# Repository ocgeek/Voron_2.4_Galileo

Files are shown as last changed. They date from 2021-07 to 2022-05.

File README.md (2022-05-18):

**Galileo Clockwork**

Please go to the original repository for Galileo Clockwork (as it is actively maintened there)
https://github.com/JaredC01/Galileo

**Galileo driven Z-Drives**

The source components are from the great **project and design** of **JaredC01** (see Voron Discord)

**Mind that these components are by design of the author a TIGHT FIT** 
Some pressing in of the bearings is expected and IMHO intended.
I used a long exagonal key driver (M10) to press them in by my body weight..

You can reach out in Voron Discord i'm **oc_geek V2.1064 V2.1820**

This is goint to be my second Voron 2.4 build 
and il will be equipped with Galileo Z Gearboxes and Galileo Extruder (and few other mods :-) ) 

I made some chages to his design (was tailored for Voron 2.2 in ~ 2020)
- Fixed the hole height of M5x40 screw to grab 5mm on the M5 post insert nut
- The Mount has a larger center hole (now ID is 8.6mm) to allow the bearing removal and avoid D shaft rubbing plastic
- Reduced the 4xM3 holes in the Mount to ID 3.4 mm (from 4.2) for a snug alignment to the Gearbox shelve
- The Mount (aka Foot) is now 10 mm taller to better suite a V2.4 build bottom height (it does not change the belts lenght)
- Stepper Spacer has now a hook (with M5x20 BH) to the inner frame extrusion so stepper Motor weight does not load on Gearbox. A hole for the M3 pass through screw has been added to the spacer for mounting the Gearbox shelve
- Added skirts for V2.4 300mm including a rotating gear (pressure) mounted on the D-Shaft protruding out of Mount front (~ 3mm)

I developed all those changes in **Fusion 360**
The **CAD file** is too large to store here 
i uploaded it on Google Drive (lates update 11st July 2021) [Z Drive f3z archive](https://drive.google.com/drive/folders/1R-tB0uDWe6UOru6ewyngyY7uPnOx-Cvc?usp=sharing)

**Z Gearbox** BOM
_Quantity is for ONE (1) Gearbox_
- 10T metal Spur Gear x1 - <<https://www.aliexpress.com/item/4000299898525.html>>
- 5x4mm Heat inserts x8 (Voron BOM)
- 60mm Long 5mm OD D-shaft (Voron BOM)
- 16T "Prusa Stile" Pulley with Base H=6mm (thinner than POWGE) x1 - e.g. <<https://www.amazon.it/gp/product/B07T5CYBJW/ref=ppx_yo_dt_b_search_asin_title?ie=UTF8&psc=1>>
- 1.0mm shim M5 washers x2 (or 0.5mm if you wanna play finer) 
- F695 2RS Bearing x4 (Carrier and Gearbox)
- F625 2RS Bearing x1 (Mount)
- M3x12mm SHCS screws x4 (to close the gear Shelves)
- M5x16mm BHCS screws x3 (gears to carrier)
- M3x18mm SHCS screws x4 (connect to the Stepper)
- M3x20mm SHCS screws x4 (connect Mount to gear Front Housing)

Mounting a Z-Drive to the frame requires:
- M5x40mm SHCS screw x1 (Mount part to Frame from where the rubber foot is)
- M5x16mm BHCS screws x2 (Mount part bottom two holes to Frame)
- M5x20mm BHCS screws x1 (Accent Spacer to Frame)

See in the **Assembly folder** there are some notes on how i did put these things together :)



These are the assembled GearBoxes



I modified the spacer so that it hooks onto the frame and sustains the Stepper weight. 
Also it sists in the center of mass of the assembly
This is reccomended works very well



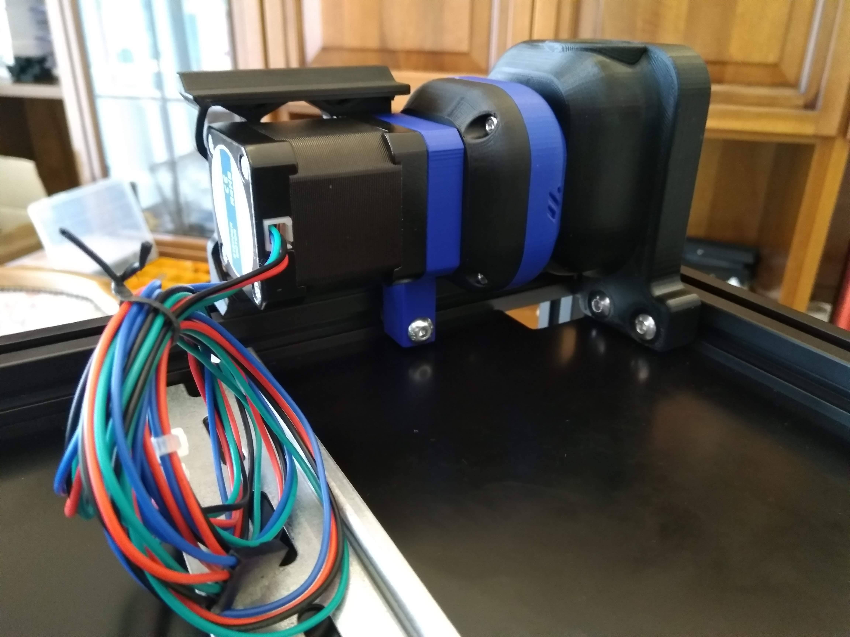
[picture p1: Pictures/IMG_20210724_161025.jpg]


I amended the Mount (foot) to be 10mm taller and better suited to the Voron 2.4 (the change does not change the belt lenghts) 









IMG_20210814_064714 (1)



**This is a list of what i ended up installing in this build :)**

**Frame and Panels:**
- 4mm thick polycarbonate panels (including the bottom deck to view through the electronics)
- Doors with hinges
- Handles 2x on top and 2x at bottom sides (it's 50Kg this thing...)

**Control Electronics and cabling**
- Duet Mini 5+ Wifi
- Duet 2+ expansion (to reach 7 drivers)
- Prepared for an additional Duet 5+ (not yet installed for ERCF MMU unit - future) via FD-CAN bus
- Duet Tool Board 1LC (v1.1 with included accelerometer) mounted on the tool head side and connected via FD-CAN bus
- Heluflon FEP wires (AWG 18, 20, 24)
- MDPC-X sleeve (used out of the chains)
- Wago 221 connectors
- Chamber temp / humidity sensor (DHT21)
- Ambient temp thermistor
- Various cable management brackets (made in Fusion360) and cables routing guide out of the cables hole in the back

**Mechanics and movement:**
- OMC Steppers-online motors
- 1.8* on Z axis (4)
- 0.9* on X-Y axis (2)
- LDO pancake for Galileo Clockwork Extruder
- Galileo gear-boxes for Z movement (required redesign of the entire skirts)
- Galileo Clockwork (Coupler Edition) for Extruder
- MGN-12 single rail on X axis
- AB-BN 30 tool body with 5015 work cooling fan
- Hall effect end stops for X/Y
- MGC5 spherical Z joints
- Klicky probe (instead of the inductive Z sensor) for bed leveling and final Z0 setting
- Pin mod on all bearings / idlers (5mm pins replace M5 screws - requires specific printed parts)

**Air Filtering**
- Nevermore Micro recirculating active carbon filter (dual 5015 fan located under the heated bed; also serves as quick chamber heat distribution in the pre-print phase)

**Lights:**
- WS2811 (aka neopixel) addressable LED strips with controllable brightness and color for each LED on each strip
- 15 LEDs on front, 18 LEDs each side top

**Others:**
- Purge bucket with scrub
- Align stands for the steel flex plate (two embedded in the Purge bucket body)

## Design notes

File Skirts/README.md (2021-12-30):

One note on the skirts...

Remind to install the **Side Skirt BEFORE** you install the Galileo GearBox itself... don't ask how do i know that...

You are adviced

These skirts are my design and will fit on a **Voron 2.4 300**



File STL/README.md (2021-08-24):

Here i uploaded the STL files for the Galileo GearBoxes 
and also the other Mods which i did implement. 

Some of the Mods (e.g. Pinned and Spherical Joints) intersect and need specific STL(s) 
making the search of the proper files a challenge

So here they are all together

:)

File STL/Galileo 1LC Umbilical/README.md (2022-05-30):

STLs for umbilical mount for 1LC Duet (or fysect) 1.1 and above toolboard

Files ARE NOT oriented for printing so please arrange them properly on plate









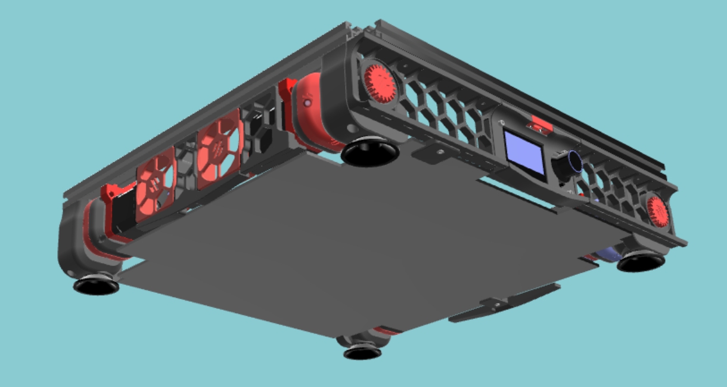
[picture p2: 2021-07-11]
Pictures/Bottom.jpg

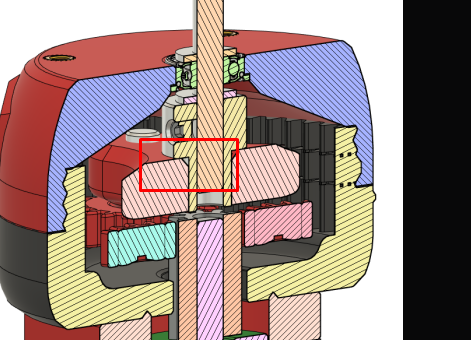
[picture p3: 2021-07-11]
Pictures/unknown.png

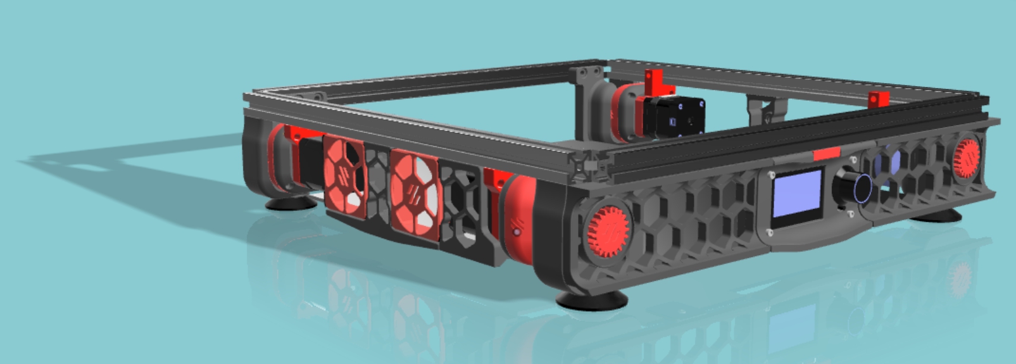
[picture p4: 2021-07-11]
Pictures/Front.jpg

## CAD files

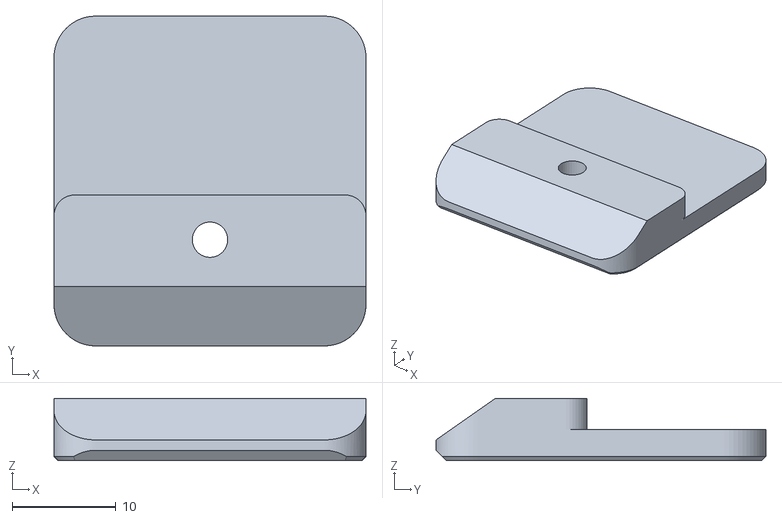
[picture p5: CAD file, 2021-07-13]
Skirts/Galileo 3mm Panel Clip x4.stl
30.0 x 31.7 x 6.00

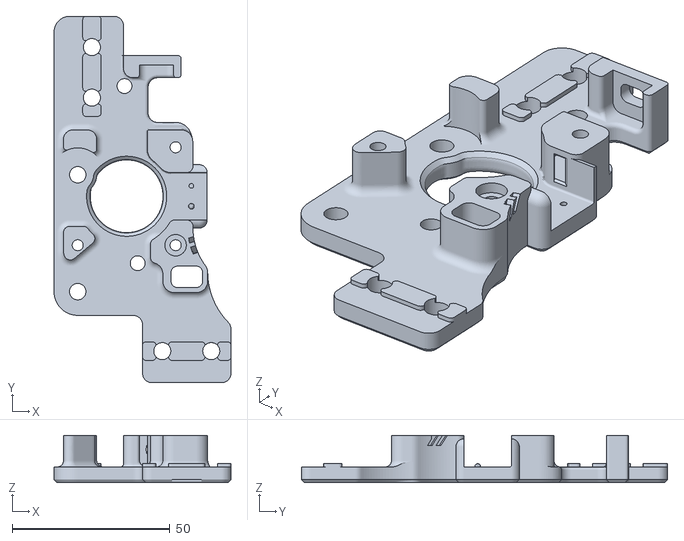
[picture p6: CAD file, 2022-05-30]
STL/Galileo 1LC Umbilical/a_drive_frame_upper_with_jst_y_endstop.stl
56.0 x 116.0 x 15.0

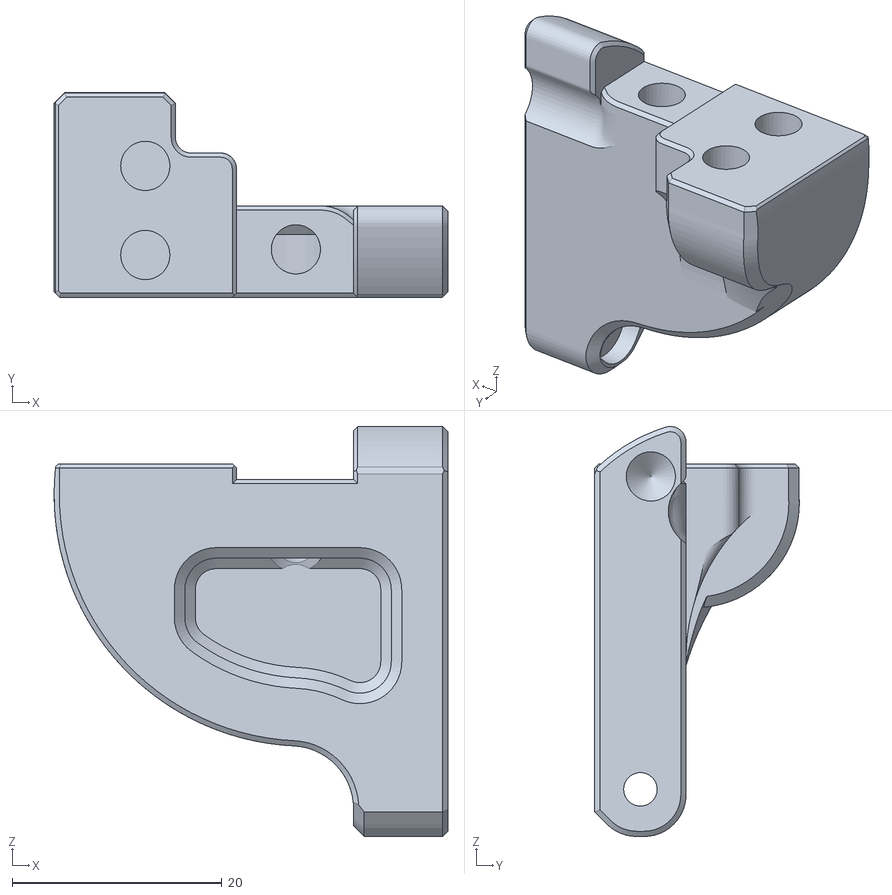
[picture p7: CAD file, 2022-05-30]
STL/Galileo 1LC/Chain anchor IGUS Backers.stl
37.6 x 19.5 x 39.1

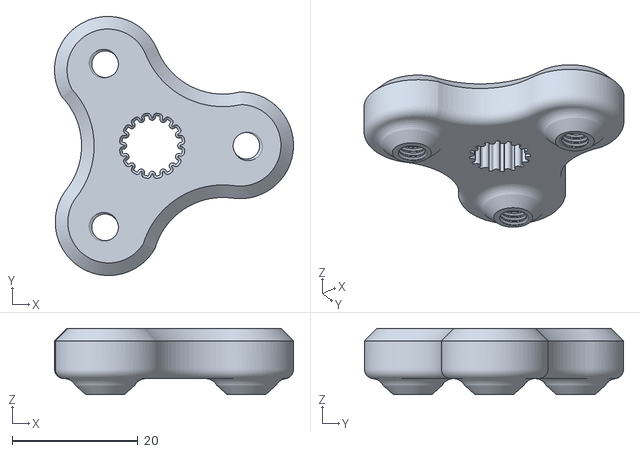
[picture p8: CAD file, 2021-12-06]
STL/GearBox Galileo/Carrier x4.stl
38.1 x 41.2 x 10.6

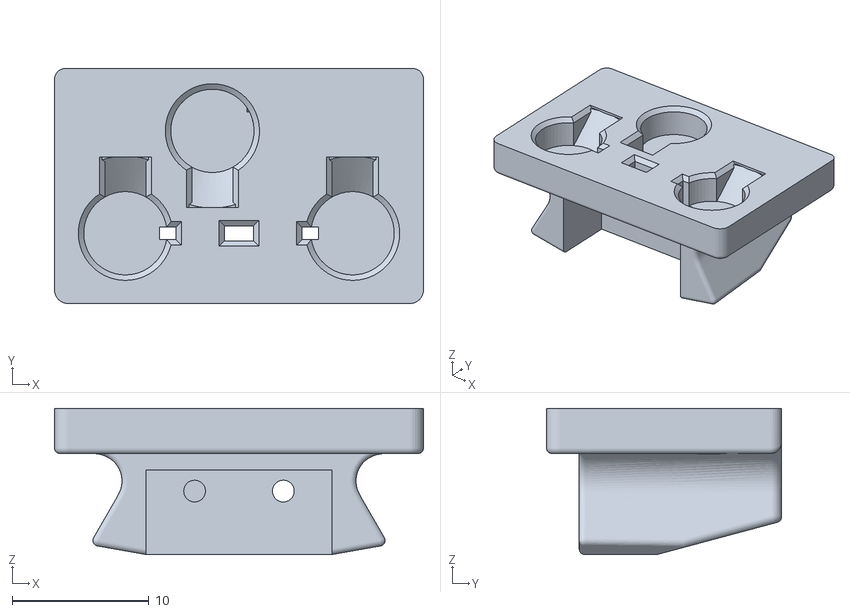
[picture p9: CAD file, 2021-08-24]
STL/Klicky for MGN12/New Probe V2 Angled.stl
27.0 x 17.2 x 10.7

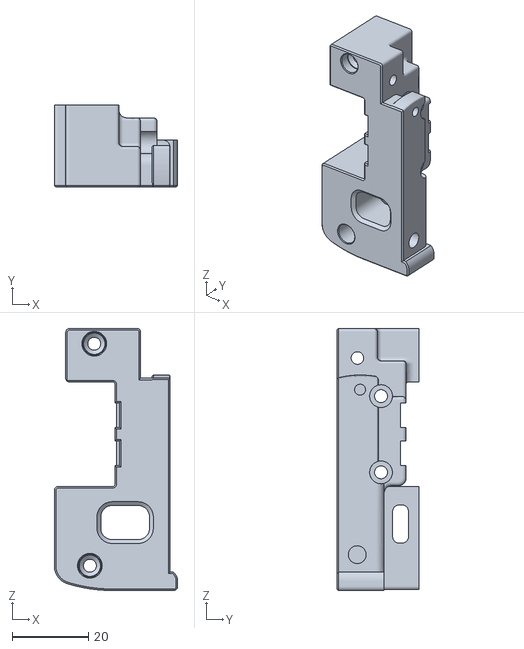
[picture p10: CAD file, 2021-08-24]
STL/MGN12 rail and Pinned Mod/x_carriage_frame_left 210729.stl
32.4 x 21.6 x 68.8

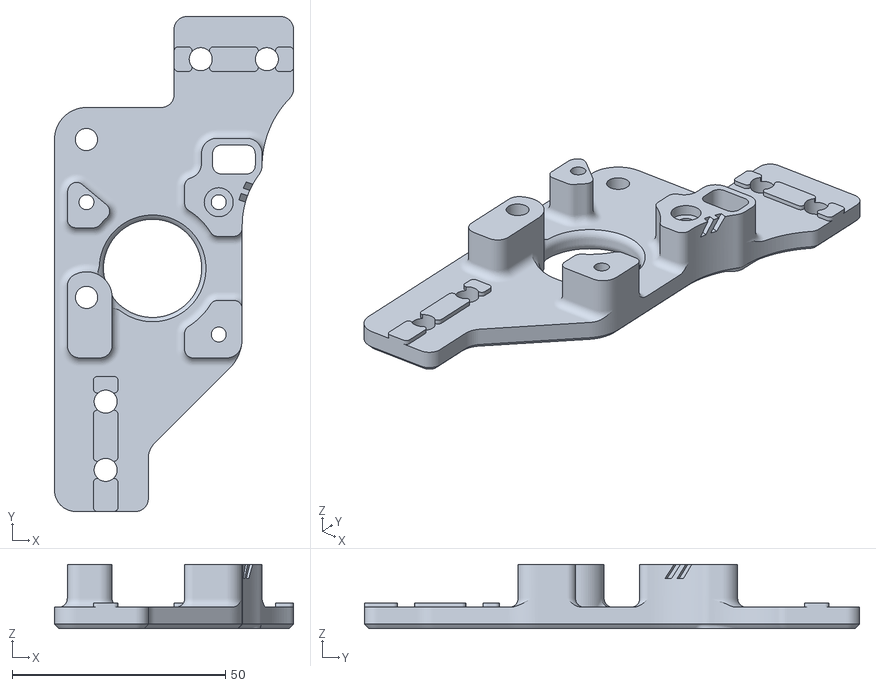
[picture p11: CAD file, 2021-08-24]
STL/Spherical Joints MGC5 and Pinned Mod/b_drive_frame_upper_pinned.stl
56.0 x 116.0 x 15.0

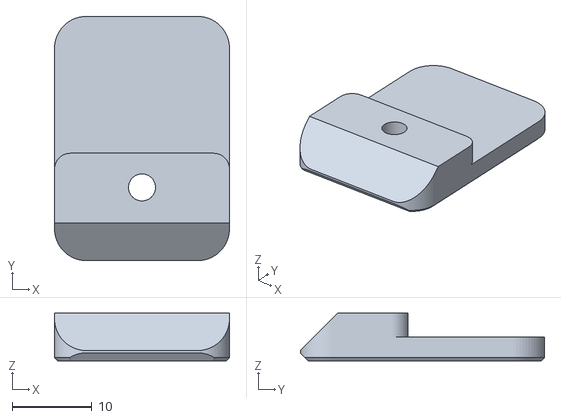
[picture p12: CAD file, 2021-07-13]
Skirts/Galileo 3mm Panel Clip Slim x2.stl
22.0 x 30.7 x 6.00

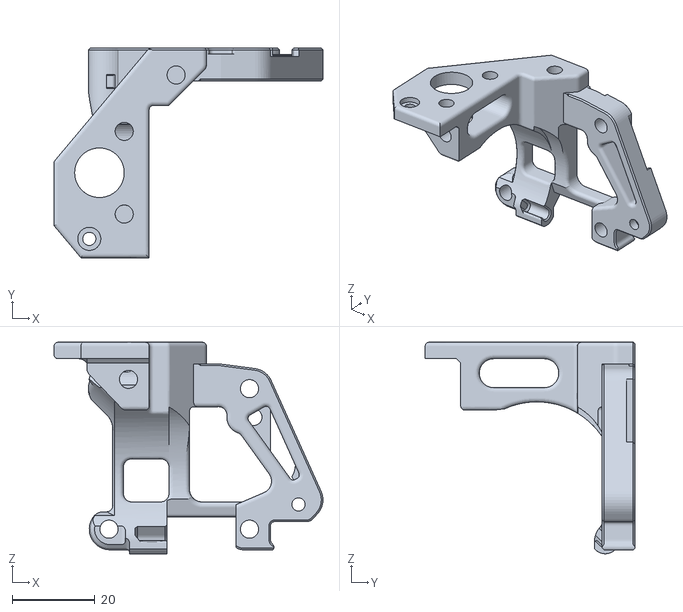
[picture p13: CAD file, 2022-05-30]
STL/Galileo 1LC Umbilical/Galileo 1LC PCB Holder Umbilical.stl
65.1 x 50.8 x 51.2

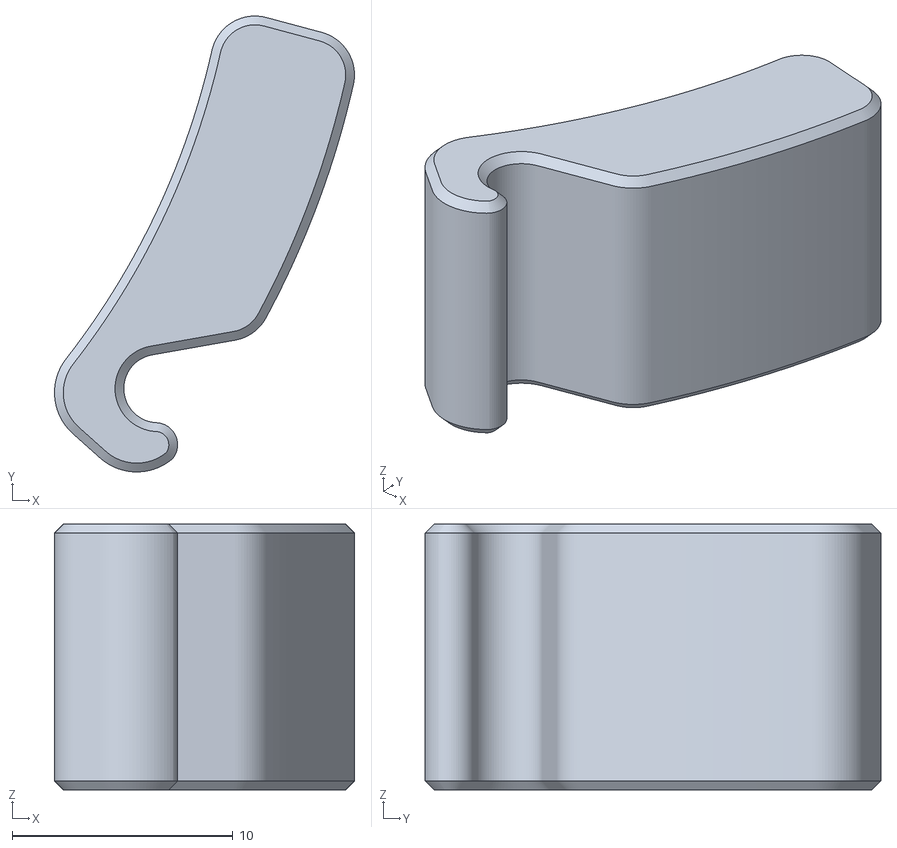
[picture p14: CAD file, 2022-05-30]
STL/Galileo 1LC/[a]_latch_shuttle.stl
13.6 x 20.7 x 12.0

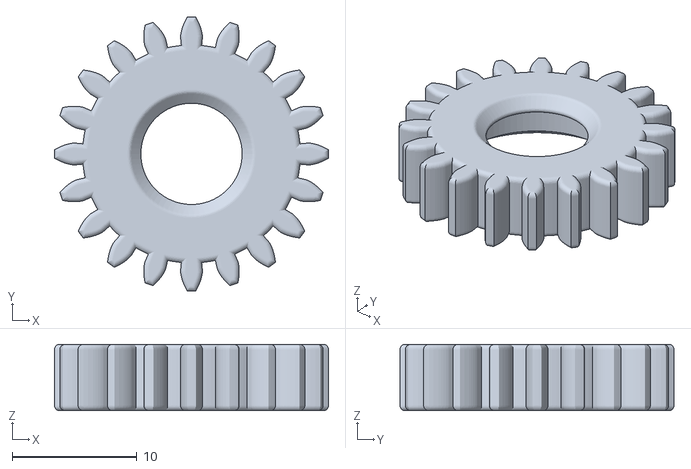
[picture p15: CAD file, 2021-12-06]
STL/GearBox Galileo/Planetary Gear x12.stl
22.0 x 22.0 x 5.33

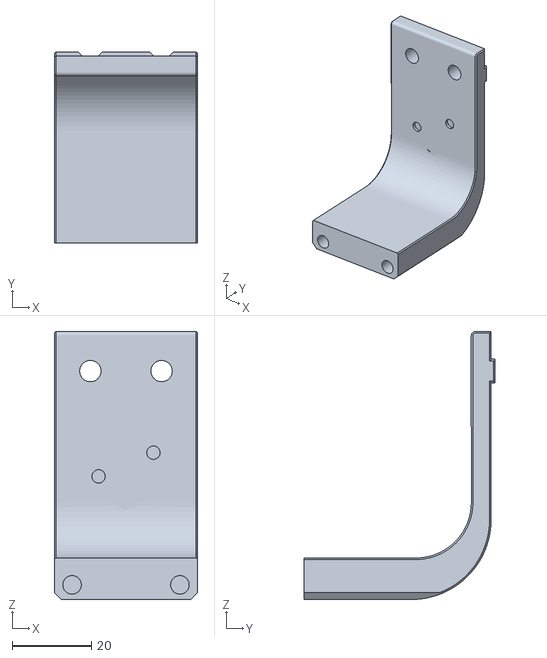
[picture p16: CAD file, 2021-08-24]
STL/Klicky for MGN12/Dock Fixed Mount 1 deeper 4 shorter with Logo - MGN12.stl
36.3 x 48.3 x 67.7

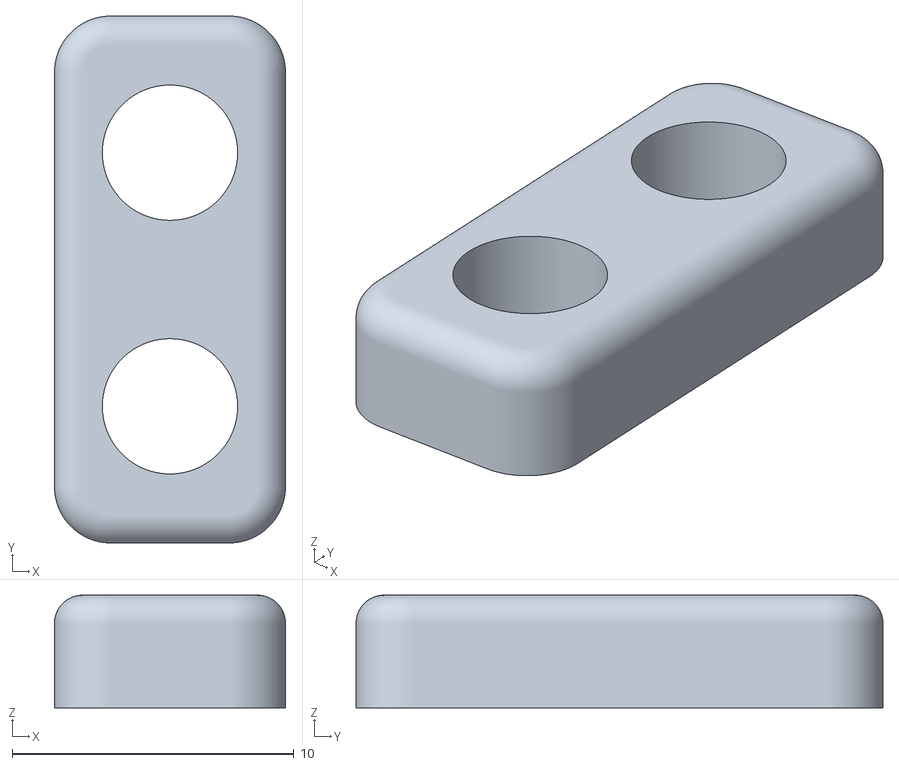
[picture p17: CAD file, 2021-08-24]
STL/MGN12 rail and Pinned Mod/probe_retainer_bracket_9mm.stl
8.20 x 18.7 x 4.00

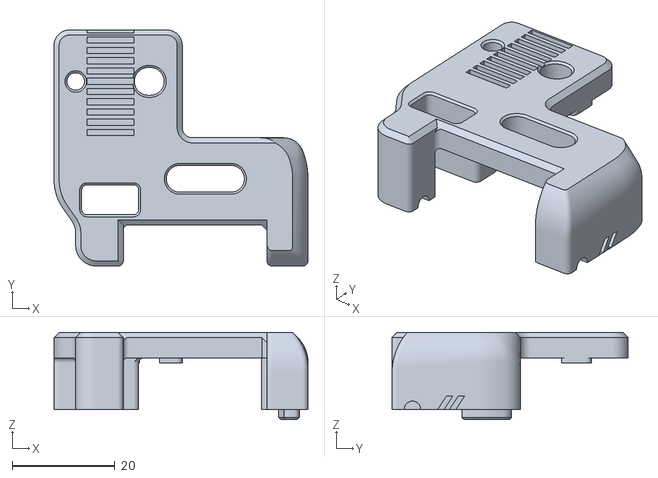
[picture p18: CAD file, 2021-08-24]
STL/Spherical Joints MGC5 and Pinned Mod/b_idler_lower_g5ec_offset_pinned.stl
49.5 x 46.0 x 17.0

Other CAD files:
Skirts/Galileo Middle Fan Support.stl
STL/Galileo 1LC Umbilical/PG7 M12 inner threads.stl
STL/Galileo 1LC/[a]_idler_guide.stl
STL/GearBox Galileo/Ring Gear Housing V2 x4.stl
STL/Galileo 1LC Umbilical/Galileo anchor Umbilical.stl
STL/Galileo 1LC Umbilical/[a] 1LC 1.1 Cover Reloaded.stl
STL/Galileo 1LC Umbilical/[a] Galileo_1LC_Top_cover Umbilical.stl
STL/Galileo 1LC Umbilical/front_body_coupler_nut_trap SB.stl
STL/Galileo 1LC/PCB Holder Backers v3.stl
STL/Galileo 1LC/Rear_Plate with chain.stl
STL/Galileo 1LC/[a] 1LC 1.1 Cover Reloaded.stl
STL/Galileo 1LC/[a] 1LC Mount Cable Cover.stl
STL/Galileo 1LC/[a]_filament_latch_coupler.stl
STL/Galileo 1LC/front_body_coupler_nut_trap.stl
STL/Galileo 1LC/x_carriage_frame_left nut trap.stl
STL/Galileo 1LC/x_carriage_frame_right nut trap.stl
STL/GearBox Galileo/Gearbox Mount L V2 x2.stl
STL/GearBox Galileo/Gearbox Mount R V2 x2.stl
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

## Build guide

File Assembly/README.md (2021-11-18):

**Mind that the Galileo Z-Drive components are by design of the author a TIGHT FIT**
Some pressing in of the bearings is expected and IMHO intended.

I try to describe here how i do assemble the Z-Drives (i did this already on two printers) and highlight some notes i took along the path of doing that




The connection to the Stepper motor is from the inside of the Z-Gear so you would need this done first...

1. Assemble the star gear onto the Stepper axle 
Mind that you have ~ 26 mm max of clearance to the carrier and you don't wanna hit it or be too far from it as you want good contact with the planetary
Use thread locker here !



2. Connect the Stepper motor to the GearBox with the four bolts from the Gearbox half 
Mind the orientation of the stepper wires (as you prefer it) and the Spacer/Hook
I use a drop of threadlock on the stepper M3 holes



3. Position the bearings
- Firstly the berings in the planetary gears simply snap (click) in place 
with a decise fingers squueze and those firmly remain in place. If those are either too hard to get in or too loose...not a good sign...calibrate printer 



- Bearings in the front mount. I do press these in place with an M10 long allen key (a washer helps) and use the weight of my body over the large key to push along the perimeter of the bearing. After some convincing.. it gets in (and wont fall out or move.. ever)



- Bearing in the Z-drive case need some filing around the hole seam (it sits along the middle of the hole). After that is out of the way (cleareance is very tight) i use the same procedure as above (allen key / washer). Once the bearing is in place it shall be almost flush with the case surface





4. The Carriage GT2 pulley (de flanged) ...yeah that one need definetly pressure...lot of it.
I use a vise as a press
- Align the pulley grooves with the pulley hole grooves of the carrier
- Use a large and tall (e.g. M10) nut as a standoff on the other side of the pulley hole (the carrier bearing holders shall not be pressed by any means)

The vise shall press the standoff Nut against the carrier center and the Pulley top at the other end
Close the vise carefully checking proper alignment in the process.

I finally remove some of the plastic which will form on the other end (at the top of the pulley exit) with a nail. It works well



5. Some filing of the shalfts may be involved as always due to pulleys/ bearings / shaft tolerances



Remember the **TWO (2) M5 x 1mm Shims** one on the inside of the Z-Gear and the other at the ouside before the Z-Belt pulley
Grease everitihg at your preference (i use just a smear of grease as you may notice...)




6. Mount the Z-Belt (9 mm) pulley - use thread locker

7. Assemble the Z-Gear to the front mount

When it is assembled you shall see no gaps between parts and the Z-Belt pulley shall have an hair of a gap to the Mount bearing. If so you did well 





8. Run in

It is IMHO a good idea do perform some time run-in of the gears before going production
I do that for a few hours with a macro and a custom test config.g that runs the gears at different speeds, positions and so on
After the run-in period the gears shall be ready to deploy :)

https://user-images.githubusercontent.com/76037248/136664748-7286a03c-4e39-45d8-aa05-b229b414e4f7.mp4

That's about it

Enjoy the Planetary gears !

(i hope the above was of any help)

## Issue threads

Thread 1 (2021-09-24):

STL export sizes

Frix-x, 2021-09-24:
Hello, I tried to print the Galileo Z gearbox by curiosity and to try it on my machine (we already discussed quickly on Discord a couple weeks ago).

However using the standard "voron" print setting let the parts too small to be able to fit the bearings and pulley inside. I checked the CAD and saw that you exported the parts with the nominal size without accounting for ABS shrinking (unlike it is for all the other genuine Voron parts).
Maybe adding a disclaimer or advice to add 1-2% rescale in the slicer could avoid the problem to other who would also try to print it.

Thank you :)

ocgeek, 2021-09-24:
There is no  need to add anything and that is how Jared designed them
The hole Z drives is a THIGH FIT but it fits

On Fri, Sep 24, 2021 at 2:33 PM Félix Boisselier ***@***.***>
wrote:

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

Frix-x, 2021-09-24:
Hm that's strange as my flow is calibrated using a micrometer at 0.924 for this specific filament roll. With that setting I can push an F695 into the mobius motor plate without any problem with a snag fit.

For the galileo Z parts, I had to go down to flow 0.89 to be able to put the F695 into the accent part. Using my standard flow, I had to use a hammer and a bearing insertion tool that broke the part...

Looking at both CAD, it's not the same size (13mm vs 13.2mm), that's why I'm asking:
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

However, thank you for your answer :)

ocgeek, 2021-09-24:
I see (and know) your point
On my side i did only a bit of filing of the hole because of the seam that is in the hole itself was taking some real estate.
Again i only did that and had no issues (yes the bearing DO NEED to be pressed in and that is by design)
Same is for the bearing sitting in the foot. It is pressed in indeed (forget Mobius that's nothing compared to this one...)

The Z dirve design ain't mine...either...so...

While i was skeptical as you are now i realized that Jared designed it this way on purpose as you do not want the bearings to move at all once those are in place
If you don't like how it is go ahead and make your amendments to the CAD

Closed 2021-09-24.

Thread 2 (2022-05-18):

CAD files unavailable

madhunm, 2022-05-18:
Hello,

The link to the CAD files (https://drive.google.com/drive/folders/1DQNbAXy60l3uwEx9qxdZTg94INP0bn9f?usp=sharing) gives a 404 error.

Can you please reshare?

Thanks!

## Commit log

2021-10-05 Updates Assembly Readme
2021-10-05 Updated Readme Assembly
2021-10-05 Update README.md
    Updated readme assembly
2021-10-05 Update README.md
    Added a pointer to the Assembly folder
2022-05-30 Rename STL/1LC umbilical/README.md to STL/Galileo 1LC Umbilical/README.md
